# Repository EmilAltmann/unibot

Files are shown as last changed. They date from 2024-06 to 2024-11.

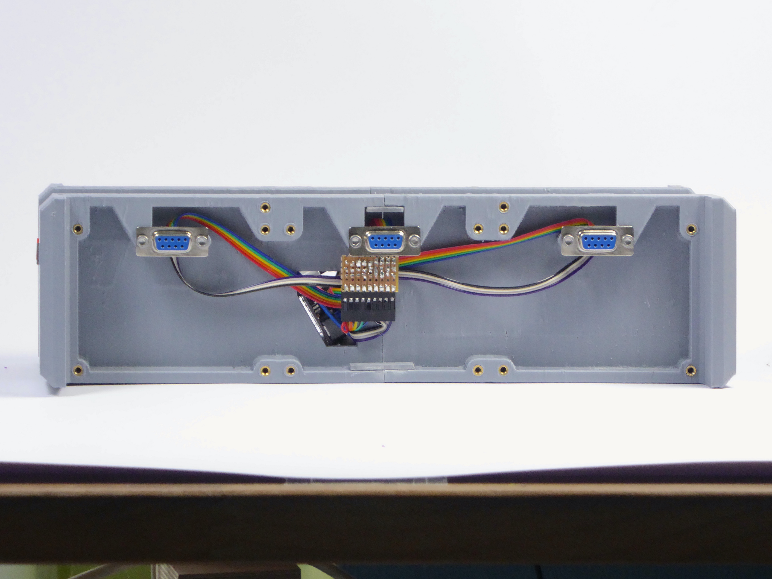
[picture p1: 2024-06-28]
chassis/pictures_chassis/chassis_rev5_side.JPG

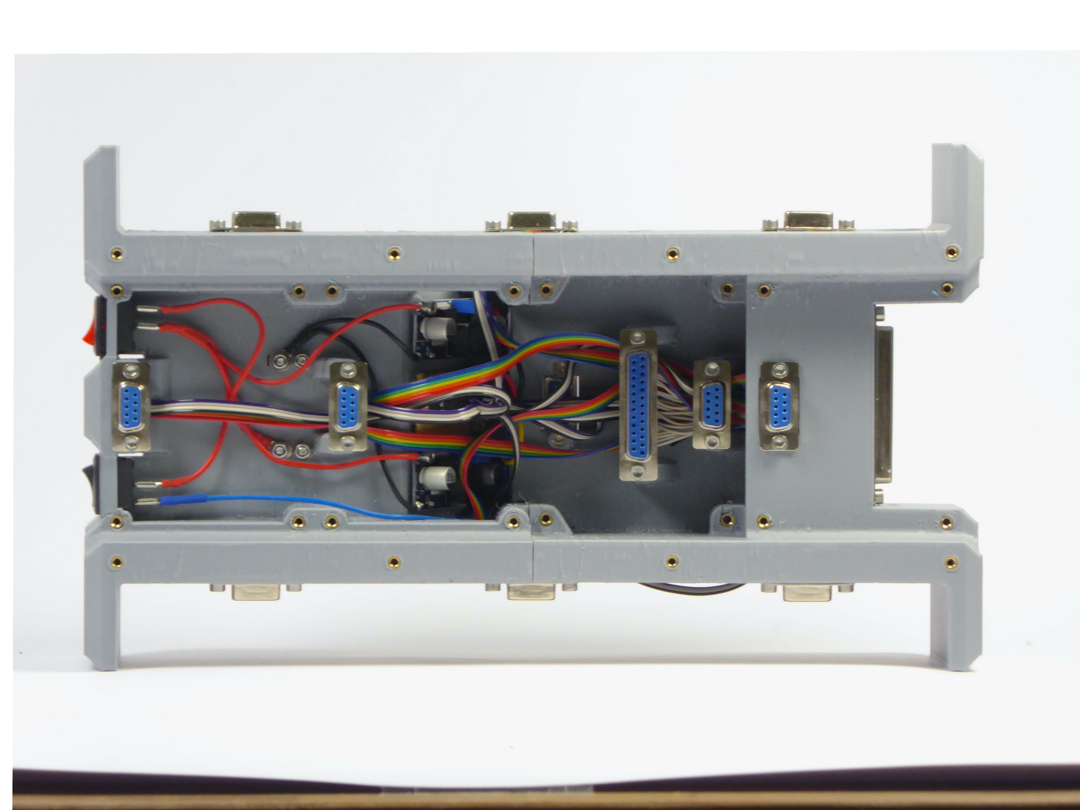
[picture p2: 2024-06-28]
chassis/pictures_chassis/chassis_rev5_top.JPG

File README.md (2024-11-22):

# unibot

This is my diploma project made in 2024 at the Universität Kassel.
The main documentation is found under unibot.pdf.

It consist out of a robot chassis with replaceable modules like different motors and sensors.

The 3D models, pictures and assembly notes for the chassis are located within the chassis folder.

Under the modules folder, you can find a collection of example modules and templates.
For most of the modules there are example codes for a raspberry pi pico located in the example_code folder.

For questions and support you can contact me under <emilaltmann@uni-kassel.de>

   Copyright 2024 Emil Altmann

   Licensed under the Apache License, Version 2.0 (the "License");
   you may not use this file except in compliance with the License.
   You may obtain a copy of the License at

       http://www.apache.org/licenses/LICENSE-2.0

   Unless required by applicable law or agreed to in writing, software
   distributed under the License is distributed on an "AS IS" BASIS,
   WITHOUT WARRANTIES OR CONDITIONS OF ANY KIND, either express or implied.
   See the License for the specific language governing permissions and
   limitations under the License.

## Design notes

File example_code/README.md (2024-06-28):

This folder contains a collection of example code.
All code is written in C for use with a raspberry pi pico.

The code should be seen as a test and example of what the modules and robots can do. 
It's not intended to be best practice advice.

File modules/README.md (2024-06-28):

# Overview over all modules:

Each module folder consists of:
- at least two pictures of the assembled module
- at least one picture of the inner electronics
- a .3mf file of the 3D printable part
- a schematic as .svg and .kicad_sch
- and sometimes a note about known insufficiencies or assembly notes

The schematics are made with KiCad 8.0.2 (https://www.kicad.org).
All 3D models should be 3D printable without supports
and with at max a 0.8mm nozzle and 0.4mm layer height.

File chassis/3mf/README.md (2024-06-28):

# 3mf files for the chassis

The main chassis consists of two parts.
Each can be printed with only minimal support (see support_for_unibot_rev5_*.png).
The models are designed to be printed with a 0.8mm nozzle at 0.4mm layer height.
The models should be arranged like seen in the slicer preview (see unibot_rev5_*_sliced.png) .

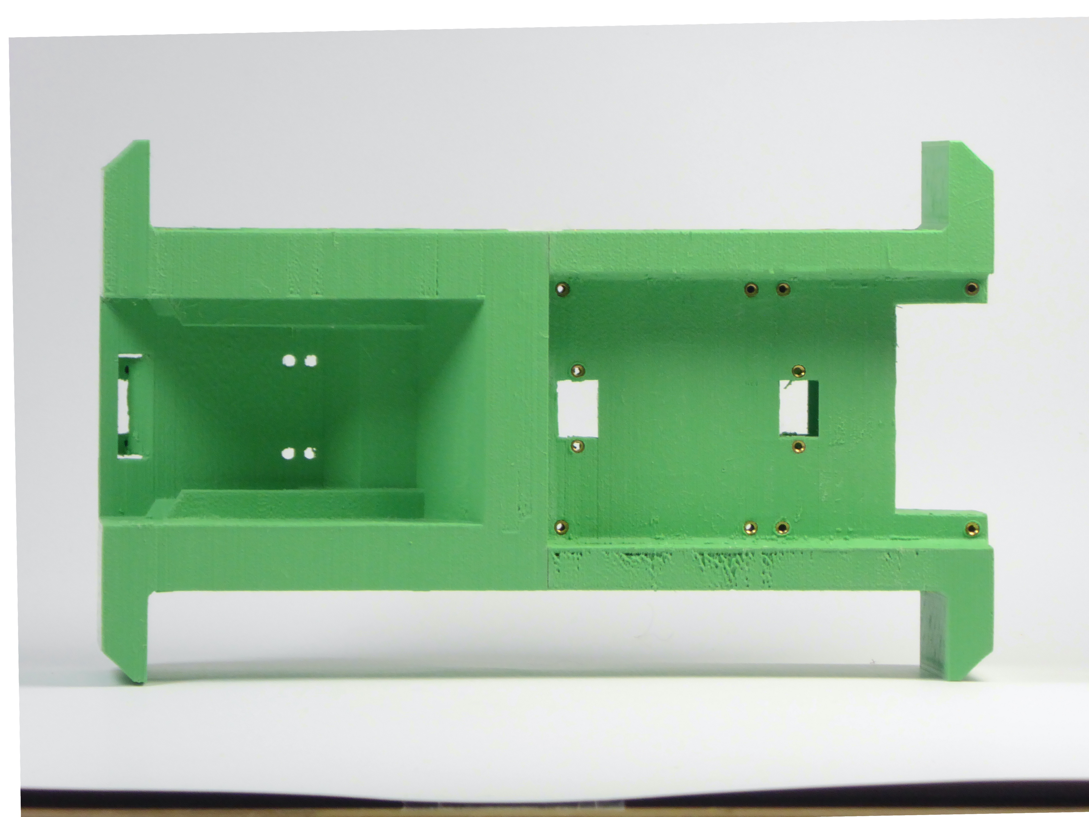
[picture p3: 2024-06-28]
chassis/pictures_chassis/chassis_rev3_bottom.JPG

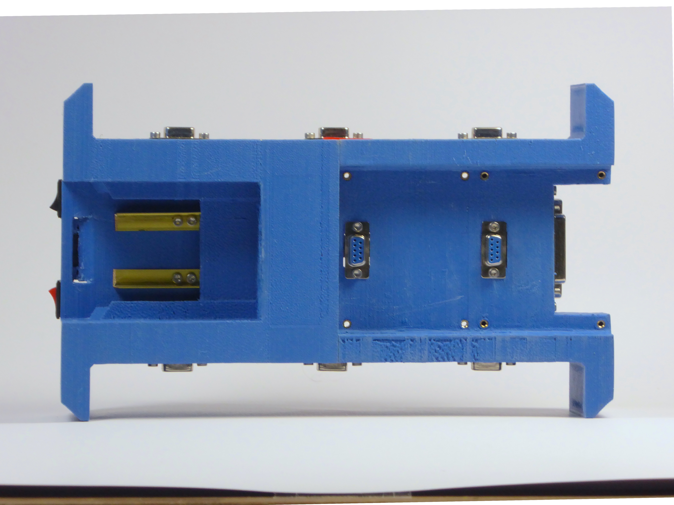
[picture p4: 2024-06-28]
chassis/pictures_chassis/chassis_rev2_bottom.JPG

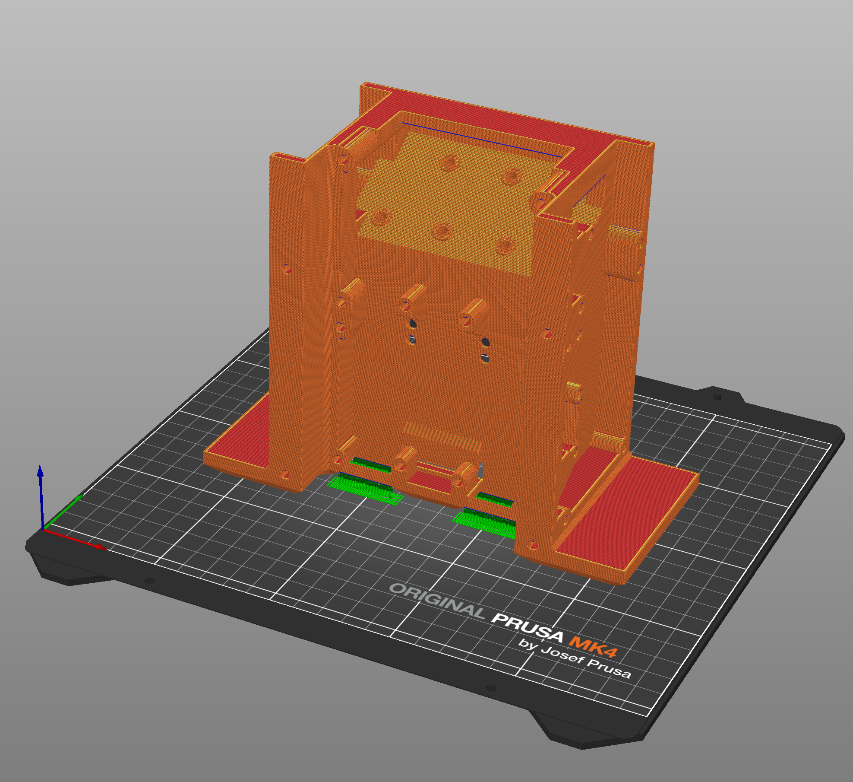
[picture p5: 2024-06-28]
chassis/3mf/unibot_rev5_back_sliced.png

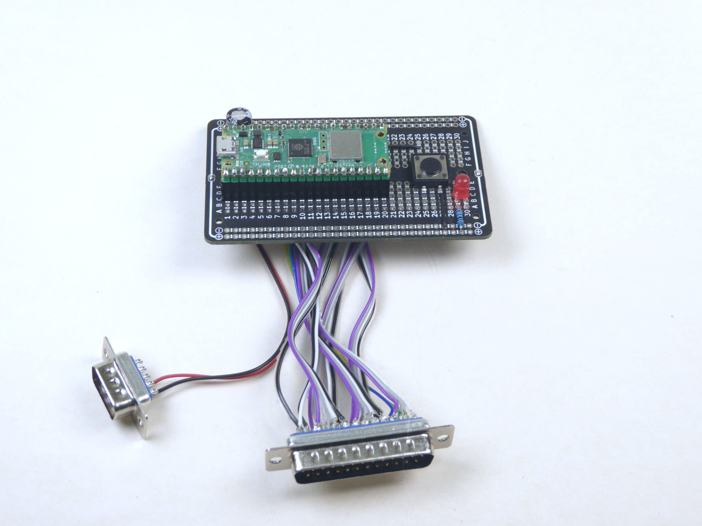
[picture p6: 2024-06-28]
modules/controller_modules/raspberry_pi_pico_w_controller_module/raspberry_pi_pico_w_controller_module_electronics.JPG

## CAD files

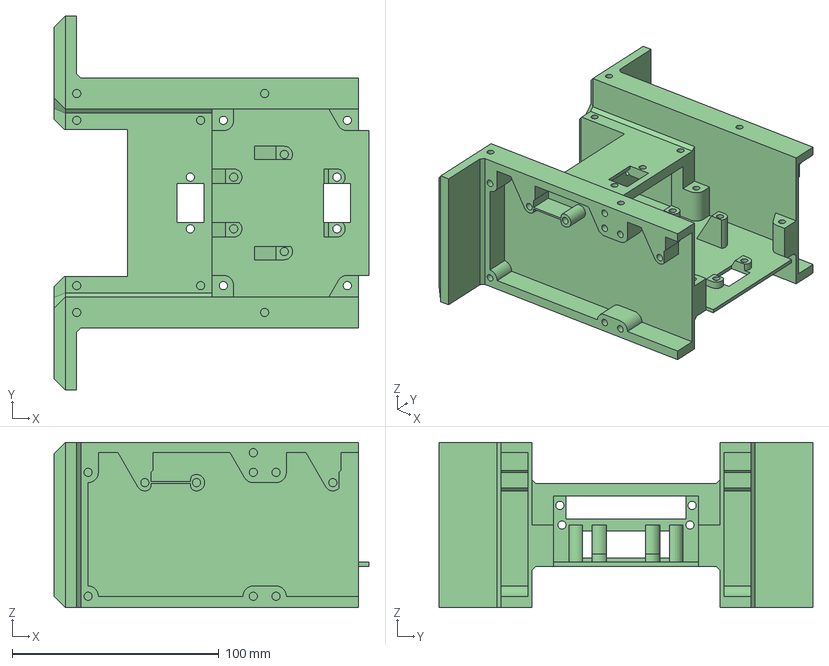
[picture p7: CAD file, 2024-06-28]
chassis/3mf/unibot_rev5_front.3mf
152.5 x 181.0 x 80.0 mm

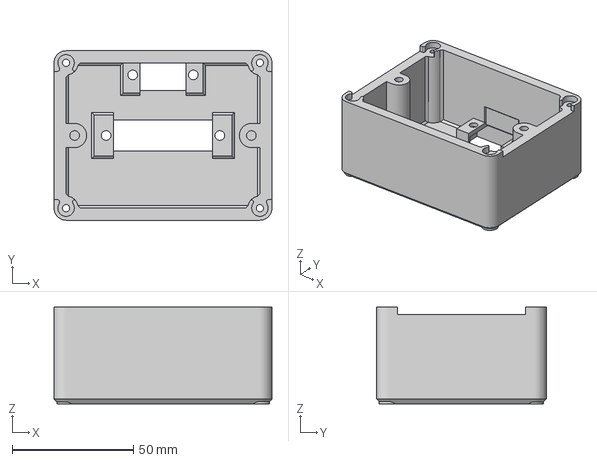
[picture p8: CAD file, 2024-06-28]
modules/controller_modules/arduino_nano_controller_module/arduino_nano_controller_module.3mf
90.0 x 70.0 x 40.0 mm

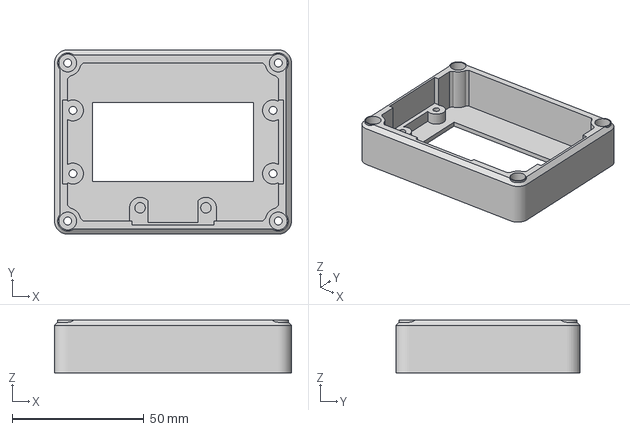
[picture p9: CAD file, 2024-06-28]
modules/display_modules/2x8_seven_segment_LED_display_module/2x8_seven_segment_display_module.3mf
90.0 x 70.0 x 20.0 mm

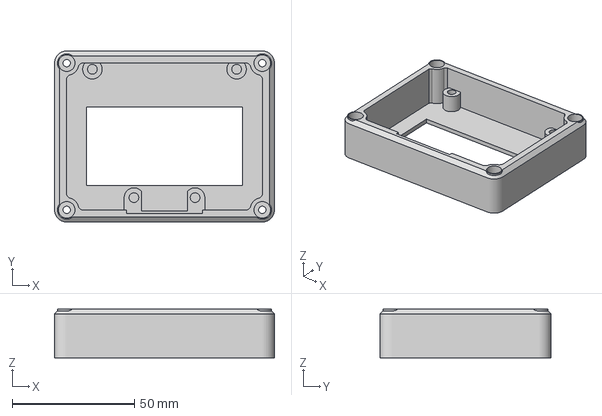
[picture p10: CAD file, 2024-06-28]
modules/display_modules/2x8x8_dot_matrix_LED_display_module/2x8x8_dot_matrix_LED_display_module.3mf
90.0 x 70.0 x 20.0 mm

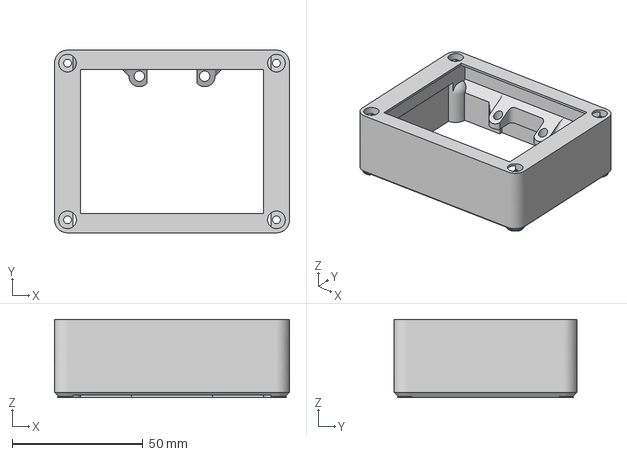
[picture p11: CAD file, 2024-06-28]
modules/display_modules/8x8_RGB_LED_dot_matrix_display_module/8x8_RGB_LED_dot_matrix_display_module.3mf
90.0 x 70.0 x 30.0 mm

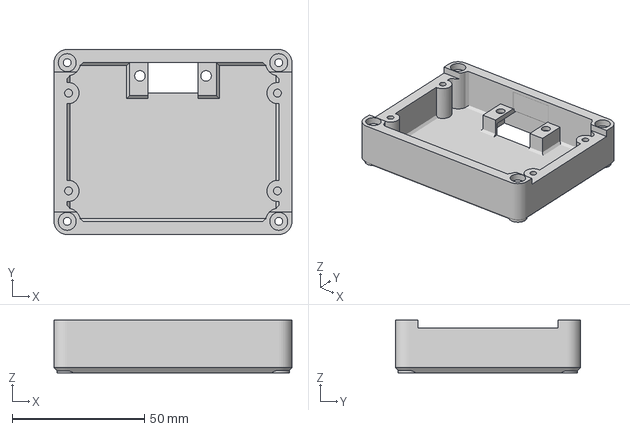
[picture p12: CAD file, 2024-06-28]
modules/display_modules/double_seven_segment_LED_display_module/double_seven_segment_LED_display_module.3mf
90.0 x 70.0 x 20.0 mm

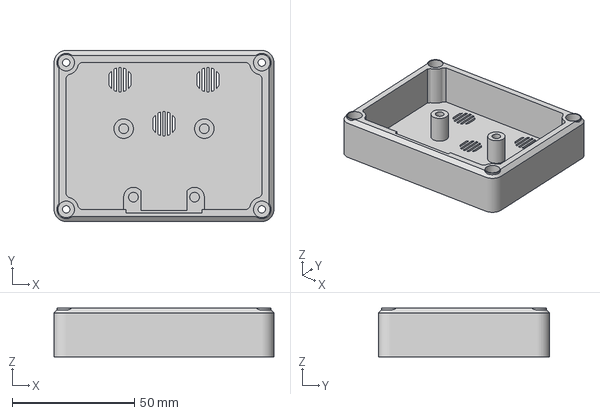
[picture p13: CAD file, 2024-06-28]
modules/interface_modules/audio_interface_module/audio_interface_module.3mf
90.0 x 70.0 x 20.0 mm

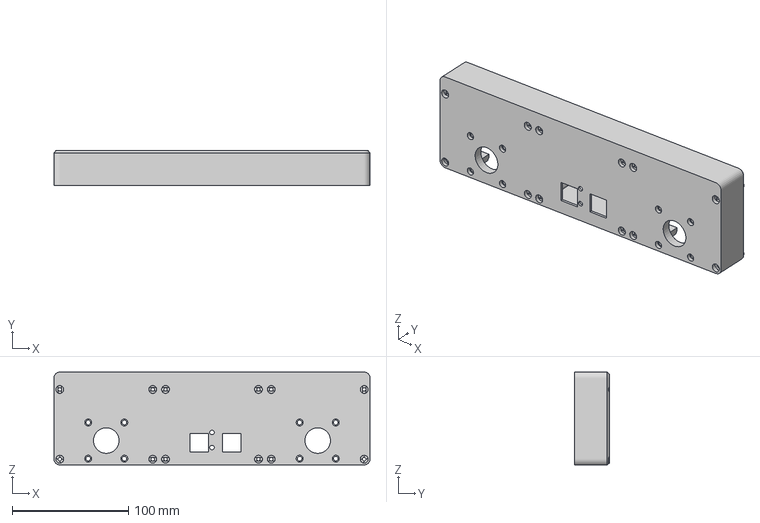
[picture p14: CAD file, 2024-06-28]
modules/motor_modules/double_stepper_motor_mecanum_wheels_module/double_stepper_motor_mecanum_wheels_module.3mf
272.0 x 30.0 x 80.0 mm

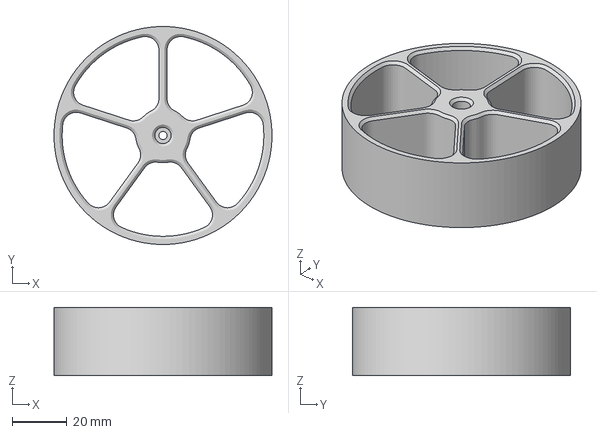
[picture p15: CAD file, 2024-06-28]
modules/motor_modules/lightweight_double_dc_motor_module/100mm_whee_for_lightweight_double_dc_motor_module.3mf
80.0 x 80.0 x 25.0 mm

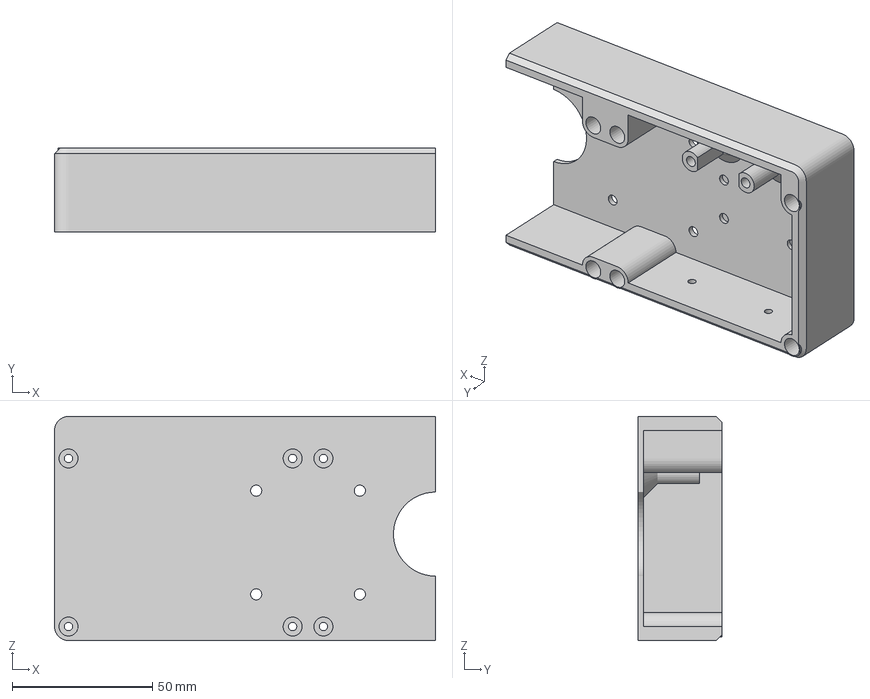
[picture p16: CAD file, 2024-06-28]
modules/motor_modules/single_dc_motor_module/single_dc_motor_module_partA.3mf
136.0 x 30.0 x 80.0 mm

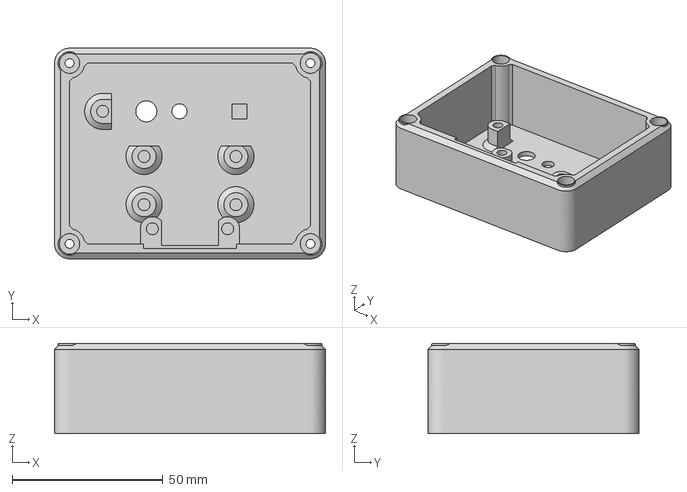
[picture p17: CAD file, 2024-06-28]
modules/motor_modules/single_lightweight_motor_module/single_lightweight_motor_module.3mf
90.0 x 70.0 x 30.0 mm

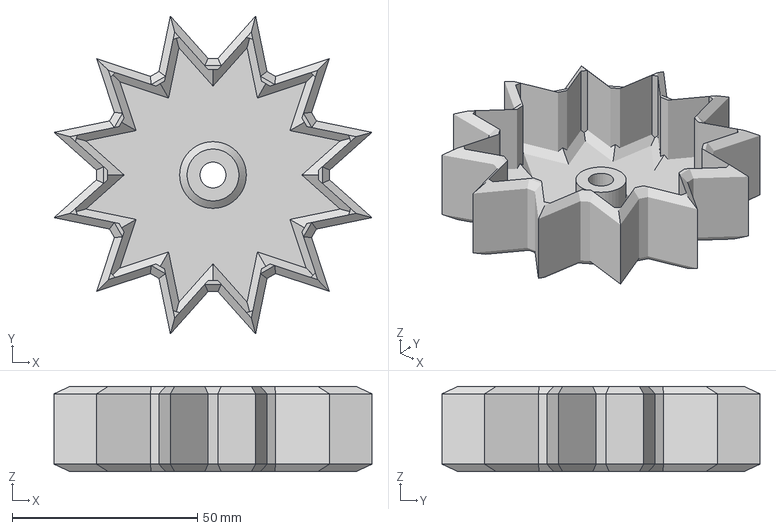
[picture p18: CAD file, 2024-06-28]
modules/motor_modules/single_motor_track_module/track_pinion_idle.3mf
85.8 x 85.8 x 23.0 mm

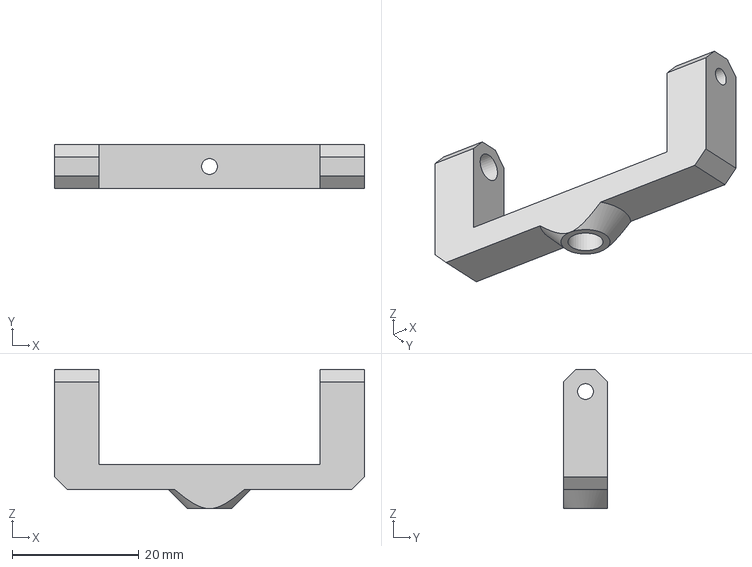
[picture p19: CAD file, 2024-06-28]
modules/sensor_modules/double_servo_ultrasonic_sensor/servo_flip_joint_for_double_servo_ultrasonic_sensor.3mf
49.0 x 7.00 x 22.0 mm

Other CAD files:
modules/display_modules/triple_bar_graph_LED_display_module/triple_bar_graph_LED_display_module.3mf
modules/interface_modules/breadboard_prototyping_module/breadboard_prototyping_module.3mf
modules/interface_modules/LCD_and_button_interface_module/LCD_and_button_interface_module.3mf
modules/sensor_modules/environment_sensor_module/environment_sensor_module.3mf
chassis/3mf/interposer.3mf
chassis/3mf/unibot_rev5_back.3mf
modules/motor_modules/lightweight_double_dc_motor_module/100mm_id_tyre.3mf
modules/motor_modules/lightweight_double_dc_motor_module/lightweight_double_dc_motor_module.3mf
modules/motor_modules/single_dc_motor_module/100mm_id_tyre.3mf
modules/motor_modules/single_dc_motor_module/100mm_wheel_for_single_dc_motor_module.3mf
modules/motor_modules/single_dc_motor_module/single_dc_motor_module_partB.3mf
modules/motor_modules/single_lightweight_motor_module/100mm_id_tyre.3mf
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

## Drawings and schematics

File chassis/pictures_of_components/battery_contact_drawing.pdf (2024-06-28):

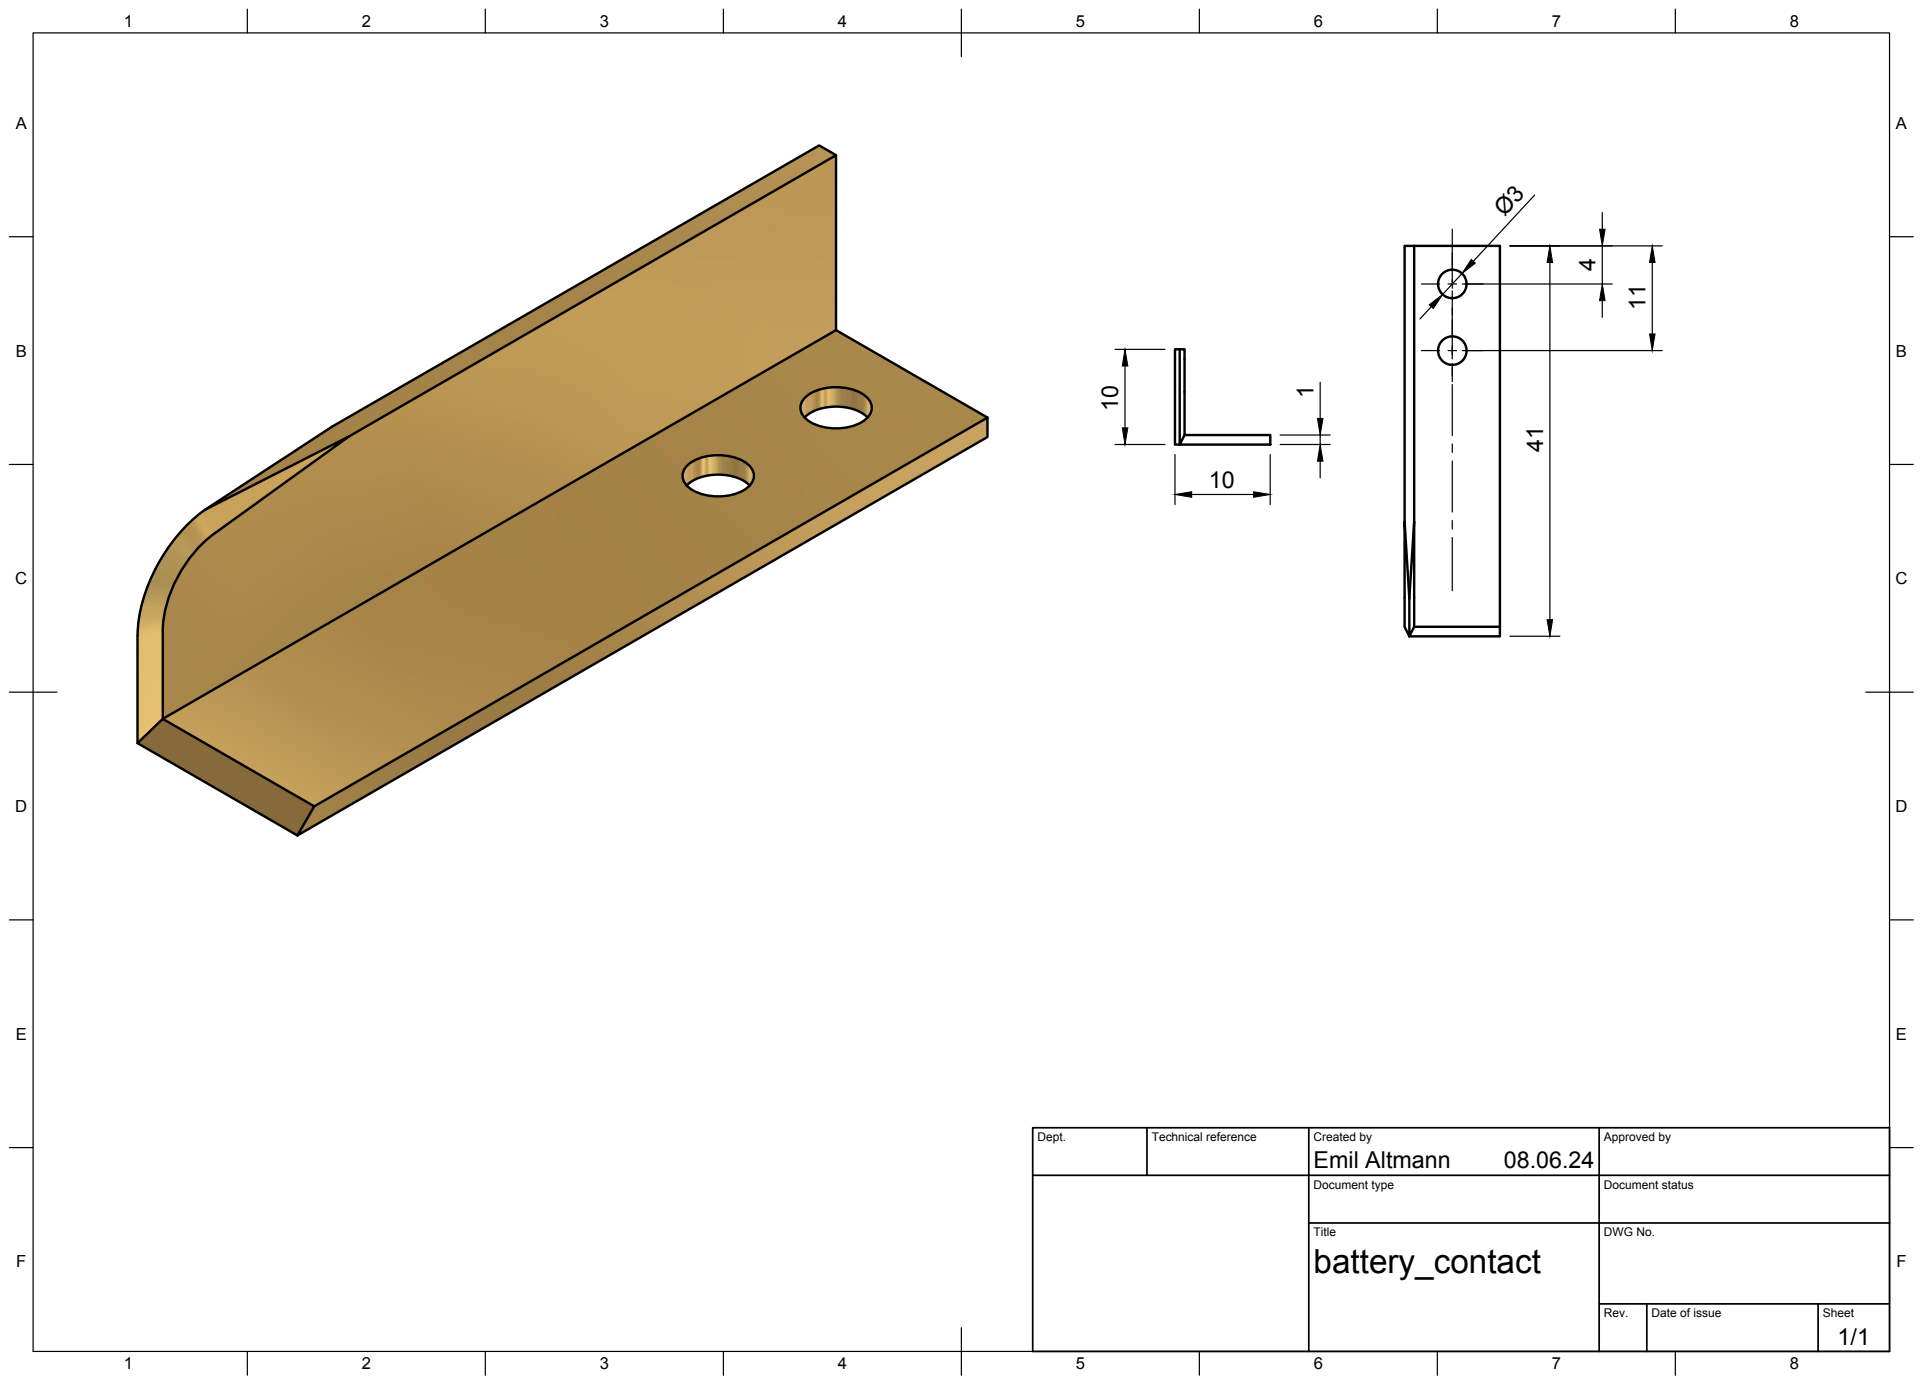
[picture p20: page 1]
Title; DWG No.; Rev.; Date of issue; Sheet

Dept. | Technical reference | Created by Emil Altmann 08.06.24 | Approved by

Document type | Document status

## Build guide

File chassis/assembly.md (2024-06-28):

# Assembly notes:

After 3D printing the two halves of the chassis can be glued together.
For increased stiffness for plastic shims can be added, inside the motor bays, as seen in all my pictures.

The 3D print needs fitting of threaded inserts in all 4mm holes (every hole you can find except the four holes for the battery contacts).
The threaded inserts are m3 with an outer dimension of 4mm by 6mm.

## Power supplies:

The next step is fitting of the power supplies.
For that you need to produce the two battery contacts (as seen in the battery_contact_drawing.pdf).
The fixation of the power cables need to be done with a washer followed by the ring terminal, another washer and a self locking nut.
The best way to insure alignment of the battery contacts is by loosely tighten the back screw and firmly tighten the front one.
Then check if the contacts can be tilted around the front screw.
With that you can align the contacts by sliding the battery pack in.
After removal of the battery pack you can tighten the screws fully.

The battery positive should be routed trow the red switch via a red cable.
from the red switch three red cables should be routed to the two lm2596 dc regulators.
Furthermore the third cable should be routed to the black switch.

The output from the black switch (+VBat) should be routed via a blue or purple cable to the distribution board.

The output from one of the regulators should be set to +5V and be routed via a red or white cable to the distribution board.

The output from the other regulator should be set to +3.3V and be routed via a yellow or gray cable to the distribution board.

Lastly the ground should be routed from the negative battery connection via a black cable to both dc regulators and (optionally throw the output of one) to the distribution board.

## All the connections:

The cable harness of the chassis consist out of 5 pieces.
There are two identical motor bay harnesses, one controller power connection, one controller data connection and the bay to interposer harness.
(see cable_harness.jpg)

The pinout and cable color of all db9 connectors should be:

	pin1 - data1 (blue)
	pin2 - data2 (green)
	pin3 - data3 (yellow)
	pin4 - data4 (orange)
	pin5 - data5 (red)

	pin6 - VBat (purple)
	pin7 - +3.3V (gray)
	pin8 - +5V (white)
	pin9 - GND (black)

- The controller power connection
	a 100mm cable for power (and no data)

- The motor bay harnesses
	a 9x5 hole PCB with a male 9 pin DuPont connector. The PCB is directly
	connected to one of the db9 connectors. The other two are paralleled
	via a 130mm cable pair to the PCB.

- The controller data harness
	two db25 connectors connected via 100mm cables.
	Wired as pin1 to pin1 ... pin 25 to pin25.

- The bay to interposer harness
	the interposer has a db37 connector with the following pinout:
	
	TopFront 120mm power and 60mm data connected to DB37 pin(1-5)
	TopMiddle 60mm power and 200mm data connected to DB37 pin(6-10)
	TopBack 130mm power and X270mm data connected to DB37 pin(11-15)

	BottomFront 120mm power and 60mm data connected to DB37 pin(32-36)
	BottomMiddle 60mm power and 120mm data connected to DB37 pin(27-31)

	LeftMotor 100mm power and 200mm data connected to DB37 pin(22-26)
	RightMotor 100mm power and 200mm data connected to DB37 pin(16-19 & 37)

	pin 20 and 21 are not connected and reserved for 5v power (20-GND 21-5V)

	The left and right motor cables should be terminated in a 9-pin DuPont.

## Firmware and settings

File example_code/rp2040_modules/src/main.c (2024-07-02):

#include "pico/stdlib.h"
#include <stdio.h>

#include "lcd1602a.pio.h"
#include "shiftreg.pio.h"

#include "display/max7219_dot_matrix.h"
#include "max7219.pio.h"
#include "light_sensor/tcs34725.h"
#include "light_sensor/ads1115.h"
#include "range_sensor/vl53l0x.h"
#include "range_sensor/vl53l0x_lidar_scanner.h"
#include "range_sensor/hy_srf05.h"
#include "imu/adxl345.h"
#include "imu/qmc5883.h"
#include "motor_driver/l298n.h"
#include "motor_driver/dual_dc_motors.h"
#include "motor_driver/servo_lib.h"
#include "motor_driver/dual_stepper_motors.h"

#include "app_drive.h"
#include "tracked_drive.h"
#include "two_wheel_drive.h"

#include "ws2812.pio.h"
#include "display/ws2812_test.h"
#include "display/ws2812_8x8.h"

#include "hardware/adc.h"

// send data or chars to 1602 LCD
void sendData() {
	int data = 0;
	int is_data = 0;
	while (true) {
		scanf(" %x", &data);
		scanf(" %d", &is_data);
		printf("data: %x %d \n",data,is_data);
		lcd1602a_send(data, is_data);
		sleep_ms(1);
    }
}

// send chars to 1602 LCD
void sendChar() {

	int data = 0;
	int is_data = 1;
	while (true) {
		scanf("%c", &data);
		if ((data >= 0x20) && (data <= 0x7f)) {
			printf("data: %c\n",data);
			lcd1602a_send(data, is_data);
			sleep_ms(10);
		}
    }

}

int main() {

	//# alwas needed
    stdio_init_all();

	//# Example project with mecanum wheels
	//# reacting and send over USART
	// start_app_drive();


	//# Example project with tracked propulsion
	// start_tracked_drive();

	//# Example project with signle wheel dc motors
	// start_two_wheel_drive();

	

	//# Example how to use lcd1602 display
    // lcd1602a_init(0, 1, 2, 3, 26, 20);
	// lcd1602a_reset();
	// lcd1602a_print("     Hello      ",1);
	// lcd1602a_print("     World!     ",2);
	// sendData();
    

	//# Example how to send serial data to 74hc595 shift registers
	// shiftreg_init();
	// shiftreg_send(0b000000111111111111110000111111);


	//# Example for RGB sensor
    // init_tcs34725();
    // test_tcs34725();
    

	//# Example for Inertial Mesurement Unit
	// init_adxl345();
	// test_adxl345();
	
	
	//# Example for srf05/4 ultrasonic distance sensor
	// init_hy_srf05();
	

	//# Example for octuple infrared line sensor
	// ads1115_init();
	// test_ads1115();
 
	//# Example for mgnetic compass
	// init_qmc5883();
	// while(1) {
		// printf("Azimuth : %d \n", (uint16_t) get_qmc5883_azimuth());
		// sleep_ms(10);
	// }


	//# Example for smoothed pwm servo contoll
	// servo_test();
	
	
	//# Example for dual lidar scanner
	// init_vl53l0x_lidar_scanner(0,1,0x70,0x71,2);


	//# Example for simple motor driver
	// init_l298n();
	// while (1) {
		// printf("set speed to: ");
		// int left  = 0;
		// scanf(" %d", &left);
		// printf("Speed %d|\n",left);
		// l298n_set_speed(left,0);
	// }
	

	//# Example for simple motor driver
	// init_dual_dc_drive();
	// set_dual_dc_speed(30000,30000);
	// while (1) {
		// printf("set speed to: ");
		// int left  = 0;
		// scanf(" %d", &left);
		// printf("Speed %d|\n",left);
		// set_dual_dc_speed(0,left);
	// }
	

	//# Example for different 8x8 RGB led test
	//# alwas needed
	// struct pio_inst test_inst = ws2812_program_init(0, 800000);
	// clear_ws2812_current_state();
	//# choose only one
	// test_ws2812_orientation(test_inst);
	// test_ws2812_color_scrolling(test_inst);
	// test_ws2812_compass_free_running(0);
	// test_ws2812_compass(2);
	

	//# Example for stepper driver
	// init_dual_stepper_drive();
	// while (1) {
		// printf("set speed to: ");
		// int left  = 0;
		// scanf(" %d", &left);
		// printf("Speed %d|\n",left);
		// set_dual_stepper_speed(left,0);
	// }
	
	
	//# Example for max7219 ontrolled displays
	//# alwas needed
	//  struct pio_inst dotmatrix = max7219_init(17,18,19);

	//# following are for dual 8x8 dot matrix
	//# scroll trow all avaiable chars
	// while (1) {
	// 	max7219_scroll_all_char(dotmatrix);
	// }
	//# repeadedly scroll Hello World!
	// while (1) {
	// 	max7219_scroll_string("Hello World!", 100);
	// }

	//# following are for dual octuple seven segment display
	//# Example for prinitng Hello World!
	// uint8_t seven_segment_string[16] = {
	// 	0,0b10100000,0b00111101,0b00001110,0b00000101,0b0011101,0b00111100,0b00011110,
	// 	0,0,0,0b00011101,0b00001110,0b00001110,0b01001111,0b00110111
	// 	}; // "HELLo___UUorLd!_"
	// max7219_disply_array_on_2x8x8(seven_segment_string);
	
	//# Example for sending data to max27219 chips
	//~ while (1) {
		//~ int data = 0;
		//~ scanf(" %x", &data);
		//~ printf("data: %x\n",data);
		//~ max7219_send_dot_char(data);
		//~ max7219_send(data);
		//~ sleep_ms(1);
	//~ }

	// //# exapmple of servo lib
	// add_servo_at_pin(0);
	// while (1)  {
	// set_servo_to_pos(0,220);
	// sleep_ms(2000);
	// set_servo_to_pos(0,1700);
	// sleep_ms(2000);
	// }

	// //# exapmple of servo lib for five servos
	// int pos0 = 0;
	// int pos1 = 0;
	// int pos2 = 0;
	// int pos3 = 0;
	// int pos4 = 0;
	// add_servo_at_pin(APP_DRIVE_TF5_PWM,500);
	// add_servo_at_pin(APP_DRIVE_TF4_PWM,500);
	// add_servo_at_pin(APP_DRIVE_TF3_PWM,500);
	// add_servo_at_pin(APP_DRIVE_TM5_PWM,600);
	// add_servo_at_pin(APP_DRIVE_TM4_PWM,1200);
	// while (true) {
	// 	printf("new pos:");
	// 	scanf("%d %d %d %d %d", &pos0, &pos1, &pos2, &pos3, &pos4);
	// 	printf("%d %d %d %d %d\n",pos0, pos1, pos2, pos3, pos4);
	// 	set_servo_to_pos(APP_DRIVE_TF5_PWM,pos0);
	// 	set_servo_to_pos(APP_DRIVE_TF4_PWM,pos1);
	// 	set_servo_to_pos(APP_DRIVE_TF3_PWM,pos2);
	// 	set_servo_to_pos(APP_DRIVE_TM5_PWM,pos3);
	// 	set_servo_to_pos(APP_DRIVE_TM4_PWM,pos4);
	// 	sleep_ms(10);
    // }


	//# needed for stopping the RP2040 going to sleep
	while(1);
}

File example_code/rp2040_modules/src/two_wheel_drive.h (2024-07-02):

#ifndef _TWO_WHEEL_DRIVE_H_
#define _TWO_WHEEL_DRIVE_H_

#include "pico/stdlib.h"

#include "pio_tool.h"
#include "display/max7219_dot_matrix.h"
#include "max7219.pio.h"
#include "motor_driver/dual_dc_motors.h"
#include "light_sensor/ads1115.h"

/*
-------------------------------------------------------------------
| This module implements a two wheeled vihicle with following modules:
| octuple trct5000 infrared line sensor module at the bottom front
| sound interface module at the bottom middle
| duble TOF sensor at the top front
| 16x8 led dot matrix at the top middle
| 2x8 seven segment at the top back
| raspberry pi pico controller
|
| The interposer configration is as follows: 
|   left motor:
|       ena - l1 <=> gp13
|       in1 - l2 <=> gp12
|       in2 - l3 <=> gp11
|
|   right motor:
|       ena - r1 <=> gp10
|       in1 - r2 <=> gp9
|       in2 - r3 <=> gp8
|   
|   octuple tcrt5000:
|       clk - bf5 <=> gp3
|       dat - bf4 <=> gp2
|
|   sound interface:
|       analogue large mic  - bm5 <=> gp28/ADC2
|       digital large mic   - bm4 <=> gp21
|       analogue small mic  - bm3 <=> gp27/ADC1
|       digital small mic   - bmf2 <=> gp20
|       passive buzzer      - bm1 <=> gp26/ADC0
|
|   dual TOF ultrasonic:
|       s1  - tf1 <=> gp6
|       cs2 - tf2 <=> gp5
|       cs1 - tf3 <=> gp4
|       clk - tf4 <=> gp3
|       dat - tf5 <=> gp2
|   
|   dual 8x8 led dot matrix:
|       dat - tm5 <=> gp17
|       clk - tm4 <=> gp18
|       ena - tm3 <=> gp19
|   
|   dual 8xseven segment:
|       dat - tb5 <=> gp14
|       clk - tb4 <=> gp15
|       ena - tb3 <=> gp16
|
-------------------------------------------------------------------
*/

#define TWOWHEEL_LM_ENA 13  // PWM enable for left motor
#define TWOWHEEL_LM_IN1 12  // dir pin 1 for left motor
#define TWOWHEEL_LM_IN2 11  // dir pin 2 for left motor

#define TWOWHEEL_RM_ENA 10   // PWM enable for right motor
#define TWOWHEEL_RM_IN1 9   // dir pin 1 for right motor
#define TWOWHEEL_RM_IN2 8  // dir pin 2 for right motor

#define TWOWHEEL_BF_DAT 2   // data for ADC I2C
#define TWOWHEEL_BF_CLK 3   // clk for ADC I2C

#define TWOWHEEL_BM_A_LM 28 // analogue large mic
#define TWOWHEEL_BM_D_LM 20 // digital large mic
#define TWOWHEEL_BM_A_SM 27 // analogue small mic
#define TWOWHEEL_BM_D_SM 20 // digital small mic
#define TWOWHEEL_BM_BUZZER 26   // passive buzzer

#define TWOWHEEL_TF_DAT 2   // data for TOF I2C
#define TWOWHEEL_TF_CLK 3   // clk for TOF I2C
#define TWOWHEEL_TF_CS1 4   // xshut pin from TOF1 for readressing
#define TWOWHEEL_TF_CS2 5   // xshut pin from TOF2 for readressing
#define TWOWHEEL_TF_SERVO 6 // servo PWM

#define TWOWHEEL_TM_DAT 17  // data to MAX7219 led driver
#define TWOWHEEL_TM_CLK 18  // ckl to MAX7219 led driver
#define TWOWHEEL_TM_ENA 19  // load to MAX7219 led driver

#define TWOWHEEL_TB_DAT 14  // data to MAX7219 led driver
#define TWOWHEEL_TB_CLK 15  // ckl to MAX7219 led driver
#define TWOWHEEL_TB_ENA 16  // load to MAX7219 led driver

#define TWOWHEEL_HIGHSPEED 2047
#define TWOWHEEL_LOWSPEED 1047

void start_two_wheel_drive();

uint8_t bin16_to_unary8(uint16_t i);

void sweep_sound();

#endif

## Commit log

2024-06-28 First publication
    [100mm_id_tyre.3mf, 100mm_whee_for_lightweight_double_dc_motor_module.3mf, 100mm_whee_for_single_lightweight_motor_module.3mf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]
2024-07-02 added more sample projects
